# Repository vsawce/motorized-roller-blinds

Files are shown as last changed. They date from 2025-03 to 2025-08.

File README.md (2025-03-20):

# Motorized Roller Blinds
A Raspberry Pi Pico W RP2040-based smart blinds project for my apartment.

I made this for fun as well as to minimize nocturnal light bleed from my apartment's outdoor lights while allowing myself to wake up to sunlight in the morning.

This system integrates with Home Assistant and MQTT, so a dedicated Home Assistant instance with the MQTT add-on is needed

## Build / Upload Instructions
As of this markdown's commit 
### Linux
1. Clone the [pico-sdk](https://github.com/raspberrypi/pico-sdk) and [FreeRTOS-Kernel](https://github.com/FreeRTOS/FreeRTOS-Kernel) repos
    * Follow their instructions for setup
2. If not done already, create the following system variables and assign them to pico-sdk and FreeRTOS-Kernel paths
    * Example in `~/.bashrc`:
      ```
      #PI PICO SDK
      export PICO_SDK_PATH=/home/<user>/pico-sdk/
      export FREERTOS_KERNEL_PATH=/home/<user>/FreeRTOS-Kernel/
      ```
    * `source ~/.bashrc` after
3. Clone this repo
4. `cd` into this repo's root directory
5. `mkdir build`
6. `cd build`
7. Run cmake in this directory
    * **Required options/arguments**:
      * `-DPICO_BOARD=pico_w`
      * `-DWIFI_SSID="<your_wifi_ssid>"`
      * `-DWIFI_PASSWORD="<your_wifi_pass>"`
      * `-DMQTT_CLIENT_ID="<custom_client_id>"`
        * Should be a custom and unique ID for each Pico W device. You choose.
      * `-DMQTT_USER=<"home_assistant_user">`
        * Should be the helper user you created specifically Home Assistant for MQTT
      * `-DMQTT_PASSWORD=<"home_assistant_pass">`
        * Should be the helper user's password you created specifically Home Assistant for MQTT
    * Example call: `cmake -DPICO_BOARD=pico_w -DWIFI_SSID="eduroam" -DWIFI_PASSWORD="abc123" -DMQTT_CLIENT_ID="picow_0" -DMQTT_USER="mqtt_test" -DMQTT_PASSWORD="xyz123" ..`
8. **Ensure the following user-defined macros in the program are correct**
    * definitions.h:
      * In `namespace BLINDS`, make sure your window height and blinds' shaft diameter is set accurately
      * In `namespace PIN`, make sure GPIO pins are set properly
    * wifi.h (may move these to definitions.h in the future):
      * `MQTT_ADDR` - point to the IP your Home Assistant is running on
      * `MQTT_ADDR_PORT` - point to the port your Home Assistant is configured to for MQTT
      * `MQTT_POS_REQUEST_TOPIC` - if you want to set a custom MQTT topic for position request (I use `/blinds/<MQTT_CLIENT_ID>/pos_request`)
      * `MQTT_POS_JSON_KEY` - JSON key string for Home Assistant -> Pico W blinds % position command (My example json: `{"pos":"50%"}`)
9. `make main` to build once all variables are set
10. Copy `src/main.uf2` into your Pico W and start a serial terminal!

## Home Assistant Example Config
As of Home Assistant Core 2025.3.3 and Home Assistant Operating System 15.0 
</br>
* After installing MQTT add-on and creating a dedicated Home Assistant user for MQTT:
  * Settings->Devices & services->MQTT
  * Click the three dots next to the Mosquitto integration entry->Reconfigure
  * Ensure port is set correctly, and then add the dedicated MQTT Home Assistant user's credentials
  * Submit
* Use something like the Studio Code Server add-on to edit `/config/configuration.yaml` (my current config):
  * ```
    # Loads default set of integrations. Do not remove.
    default_config:
    
    # Load frontend themes from the themes folder
    frontend:
      themes: !include_dir_merge_named themes
    
    automation: !include automations.yaml
    script: !include scripts.yaml
    scene: !include scenes.yaml
    
    input_number:
      slider1:
        name: Bedroom Blinds
        initial: 0
        min: 0
        max: 100
        step: 5
    mqtt:
      - cover:
          name: Smart Blinds
          unique_id: smart__blinds
          command_topic: "/blinds/picow_0/command"
          position_topic: "/blinds/picow_0/pos_status"
          set_position_topic: "/blinds/picow_0/pos_req"
          payload_open: "100"
          payload_close: "0"
          position_open: 100
          position_closed: 0
    ```
* Set up an automation with similar YAML:
  * ```
    - id: <AUTO_ASSIGNED_BY_HOMEASSISTANT?>
    alias: Adjust Blinds Position
    description: ""
    triggers:
      - trigger: state
        entity_id: input_number.slider1
    conditions: []
    actions:
      - action: mqtt.publish
        data_template:
          qos: "0"
          topic: "/blinds/picow_0/pos_request"
          payload: "{\"pos\":\"{{ states('input_number.slider1') | int }}%\"}"
    mode: single
    ```

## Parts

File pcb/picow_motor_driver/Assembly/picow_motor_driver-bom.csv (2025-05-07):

Comment | Designator | Footprint | JLCPCB Part #（optional）
10nF | C1 | Capacitor_SMD:C_0603_1608Metric | C1589
LED | D1,D2,D3,D4 | LED_SMD:LED_0603_1608Metric | C965799
470 | R1,R2,R3,R4 | Resistor_SMD:R_0603_1608Metric | C23179
10k | R5,R6,R7 | Resistor_SMD:R_0603_1608Metric | C25804
TS-1088-AR02016 | SW1,SW2,SW3 | Library:SW-SMD_L3.9-W3.0-P4.45 | C720477
ULN2003D1013TR | U2 | Library:SOIC-16_L9.9-W3.9-P1.27-LS6.0-BL | C61273
920-E52A2021S10100 | USB1 | Library:MICRO-USB-SMD_5P-P0.65-H-F_C10418 | C10418

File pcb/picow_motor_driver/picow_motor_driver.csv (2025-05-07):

Reference | Value | Footprint | Datasheet | Qty | DNP | Exclude from BOM | Exclude from Board
C1 | 10nF | Capacitor_SMD:C_0603_1608Metric | ~ | 1
D1,D2,D3,D4 | LED | LED_SMD:LED_0603_1608Metric | ~ | 4
J1 | Conn_01x02_Pin | Connector_PinHeader_2.54mm:PinHeader_1x02_P2.54mm_Vertical | ~ | 1
J2 | Conn_01x05_Pin | Connector_PinHeader_2.54mm:PinHeader_1x05_P2.54mm_Horizontal | ~ | 1
J3 | Conn_01x04_Pin | Connector_PinSocket_2.54mm:PinSocket_1x04_P2.54mm_Horizontal | ~ | 1
R1,R2,R3,R4 | 470 | Resistor_SMD:R_0603_1608Metric | ~ | 4
R5,R6,R7 | 10k | Resistor_SMD:R_0603_1608Metric | ~ | 3
SW1,SW2,SW3 | ~ | Library:SW-SMD_L3.9-W3.0-P4.45 | https://atta.szlcsc.com/upload/public/pdf/source/20200810/C720475_60D09DD6C54279ADDB2DC25100F1CC11.pdf | 3
U1 | Pico | Library:RPi_Pico_SMD_TH |  | 1
U2 | ~ | Library:SOIC-16_L9.9-W3.9-P1.27-LS6.0-BL | https://atta.szlcsc.com/upload/public/pdf/source/20171116/C93000_15108227945891124497.pdf | 1
USB1 | ~ | Library:MICRO-USB-SMD_5P-P0.65-H-F_C10418 | https://atta.szlcsc.com/upload/public/pdf/source/20210305/C10418_4890444E73C7CF5EB311058F76E5ECA4.pdf | 1

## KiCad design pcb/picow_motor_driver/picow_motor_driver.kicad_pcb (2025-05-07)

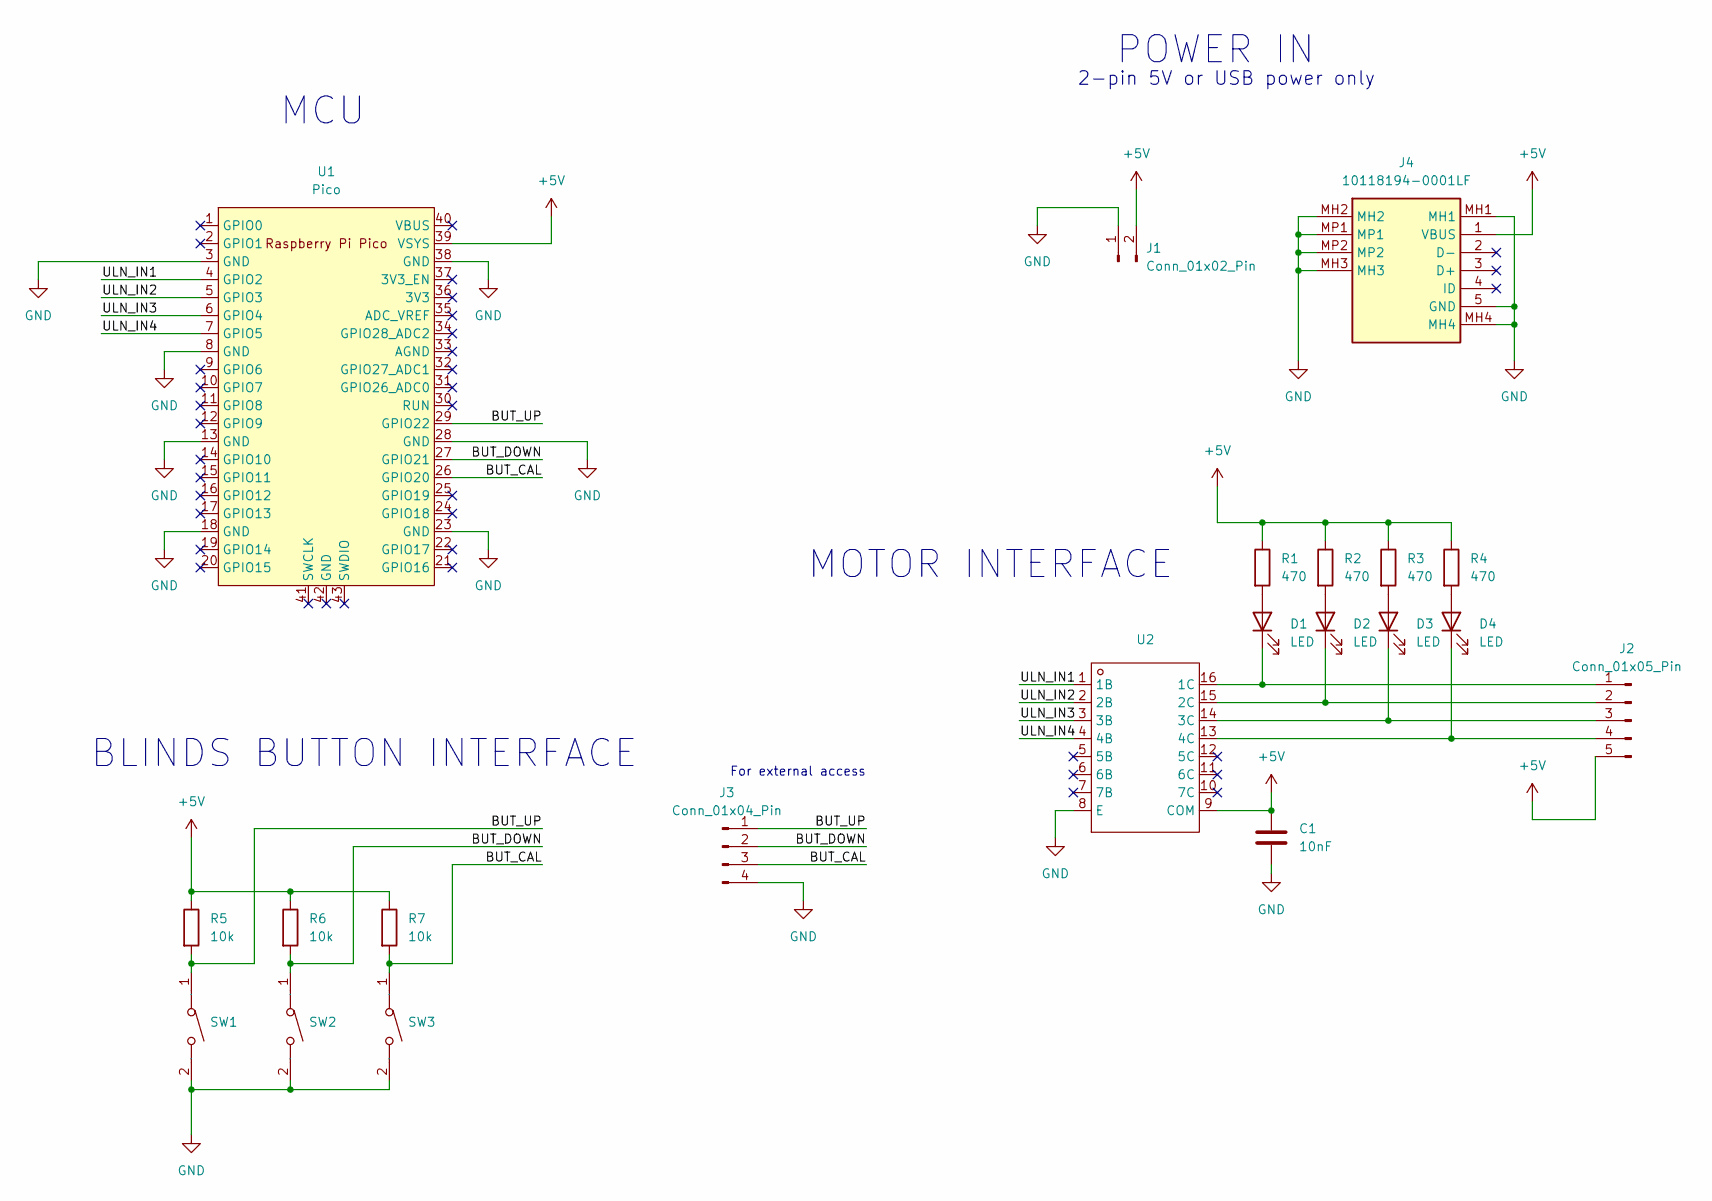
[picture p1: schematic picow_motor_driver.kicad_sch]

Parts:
C1: 10nF; C_0603_1608Metric
D1, D2, D3, D4: LED; LED_0603_1608Metric
J1: Conn_01x02_Pin; PinHeader_1x02_P2.54mm_Vertical
J2: Conn_01x05_Pin; S5B-XH-A
J3: Conn_01x04_Pin; S4BXHALFSN
J4: 10118194-0001LF; 101181940001LF; Manufacturer_Part_Number 10118194-0001LF
R1, R2, R3, R4: 470; R_0603_1608Metric
R5, R6, R7: 10k; R_0603_1608Metric
SW1, SW2, SW3: SW-SMD_L3.9-W3.0-P4.45; Manufacturer Part TS-1088-AR02016; LCSC Part Name 4*3*2mm 立贴 轻触开关
U1: Pico; RPi_Pico_SMD_TH
U2: SOIC-16_L9.9-W3.9-P1.27-LS6.0-BL; Manufacturer Part ULN2003D1013TR; LCSC Part Name ULN2003D1013TR

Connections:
+5V: C1.1, J1.2, J2.5, J4.1 (VBUS), R1.1, R2.1, R3.1, R4.1, R5.1, R6.1, R7.1, U1.39 (VSYS), U2.9 (COM)
/BUT_CAL: J3.3, R7.2, SW3.1, U1.26 (GPIO20)
/BUT_DOWN: J3.2, R6.2, SW2.1, U1.27 (GPIO21)
/BUT_UP: J3.1, R5.2, SW1.1, U1.29 (GPIO22)
/ULN_IN1: U1.4 (GPIO2), U2.1 (1B)
/ULN_IN2: U1.5 (GPIO3), U2.2 (2B)
/ULN_IN3: U1.6 (GPIO4), U2.3 (3B)
/ULN_IN4: U1.7 (GPIO5), U2.4 (4B)
GND: C1.2, J1.1, J3.4, J4.5 (GND), J4.MH1, J4.MH2, J4.MH3, J4.MH4, J4.MP1, J4.MP2, SW1.2, SW2.2, SW3.2, U1.3 (GND), U1.8 (GND), U1.13 (GND), U1.18 (GND), U1.23 (GND), U1.28 (GND), U1.38 (GND), U2.8 (E)
unnamed: D1.2 (A), R1.2
unnamed: D1.1 (K), J2.1, U2.16 (1C)
unnamed: D2.2 (A), R2.2
unnamed: D2.1 (K), J2.2, U2.15 (2C)
unnamed: D3.2 (A), R3.2
unnamed: D3.1 (K), J2.3, U2.14 (3C)
unnamed: D4.2 (A), R4.2
unnamed: D4.1 (K), J2.4, U2.13 (4C)

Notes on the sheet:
POWER IN
BLINDS BUTTON INTERFACE
2-pin 5V or USB power only
MCU
For external access
MOTOR INTERFACE

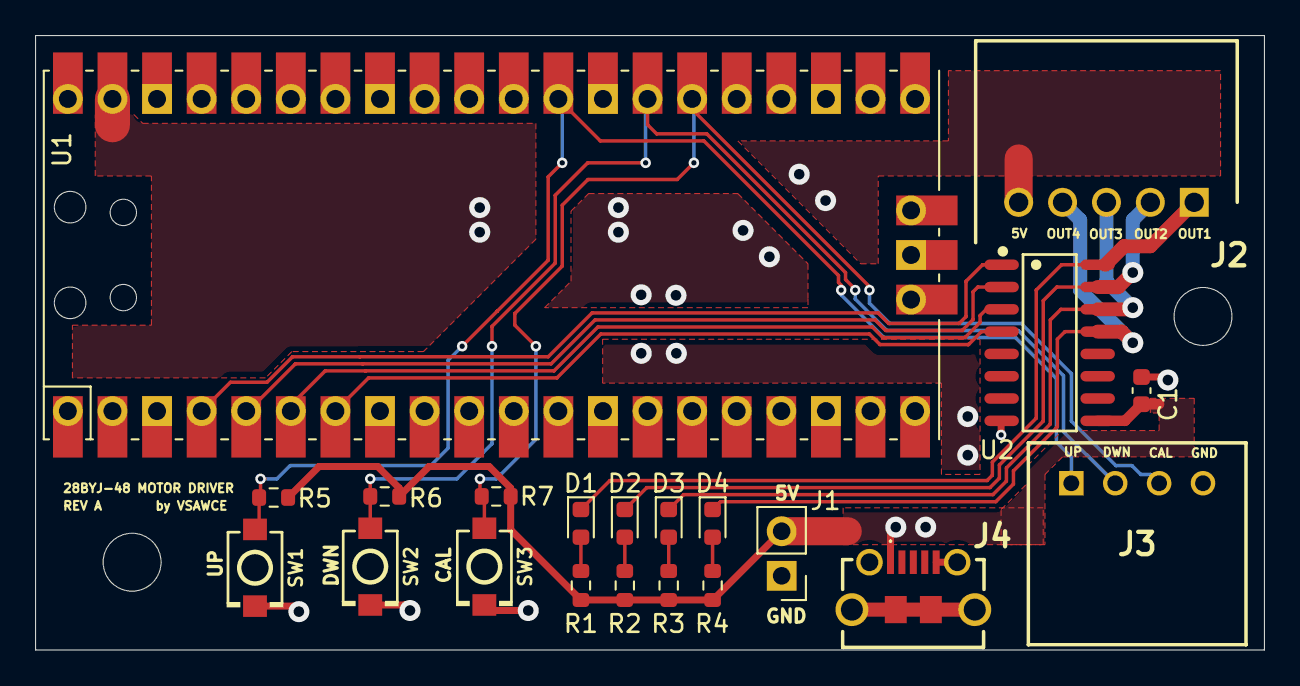
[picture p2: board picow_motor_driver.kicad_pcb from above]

Board: 2 copper layers, 70.0 x 35.0 mm, 21 parts (0 on the bottom side), 17 nets.

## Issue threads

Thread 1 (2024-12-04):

Add/test motor control in reverse direction

vsawce, 2024-12-04:

vsawce, 2024-12-09:
Added with 207ea58

Closed 2024-12-09.

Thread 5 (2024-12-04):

Finalize Google Home integration methodology

vsawce, 2024-12-04:
Pi Pico W <-> IFTTT HTTP <-> Google Home?

vsawce, 2025-03-14:
Pi Pico W (lwIP MQTT) <-> MQTT Broker (Home server) <-> Google Home

Closed 2025-03-14.

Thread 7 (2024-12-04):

RTOS Conversion and Multithreading

vsawce, 2024-12-04:
Run WiFi tasks as well as motor drives on separate threads

vsawce, 2025-01-13:
Gotta figure out allocation of functionalities between cores as well, as well as priorities

vsawce, 2025-02-12:
Good enough for now. Bound logger to 1st core, and blink/motor to 2nd core. Left wifi ambiguous as binding it throws assertions/panics, but it usually starts on the 1st core

Closed 2025-02-12.

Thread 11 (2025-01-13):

Basic WiFi functionality

vsawce, 2025-01-13:
Test ping to 8.8.8.8 (google) or something

vsawce, 2025-01-27:
[5fd85c7](https://github.com/vsawce/motorized-roller-blinds/commit/5fd85c7c6ad207df2d6783b920fc79bf568ae20f) didn't actually fix panic in NO_SYS=0 mode. Sometimes it triggers intermittently.

Potential workaround is to allow wifi initialization tasks to go first before launching other ones.

vsawce, 2025-01-27:
cyw43_arch_init must go first apparently (therefore moved wifi task to start first)? Otherwise, panics/assertions are thrown such as `assertion "!(raw_irq_mask[get_core_num()] & gpio_mask)" failed`. Need to investigate.

Closed 2025-02-12.

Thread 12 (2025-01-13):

Add USB/UART debug interface

vsawce, 2025-01-13:
Can be related to #8.

Need to figure out how to allocate this functionality to one of the two cores #7.

vsawce, 2025-01-15:
Add runtime printout!

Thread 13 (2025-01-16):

Thermistor to sense motor temperature

vsawce, 2025-01-16:
Enact shutoffs if too hot?

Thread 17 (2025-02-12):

Button debouncing

vsawce, 2025-02-12:
Related to #3. Also good to practice again

vsawce, 2025-02-25:
Integrated button actions to motor task, and debouncing probably not needed as lazy button read or motor command processing delays should be good enough as a replacement

Closed 2025-02-25.

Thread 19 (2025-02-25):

Add watchdog/timer for purpose of releasing motor

vsawce, 2025-02-25:
Add a watchdog/timer to monitor if the motor command queue hasn't received any new commands after a fixed time interval, then send a release/stop command

vsawce, 2025-02-28:
Done

Closed 2025-02-28.

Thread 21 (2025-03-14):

Implement MQTT to connect with MQTT broker on HAOS instance

vsawce, 2025-03-14:
Related: #5

Pi Pico W (lwIP MQTT) <-> MQTT Broker (Home server) <-> Google Home

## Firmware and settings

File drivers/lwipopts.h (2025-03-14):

#ifndef _LWIPOPTS_EXAMPLE_COMMONH_H
#define _LWIPOPTS_EXAMPLE_COMMONH_H


// Common settings used in most of the pico_w examples
// (see https://www.nongnu.org/lwip/2_1_x/group__lwip__opts.html for details)

// allow override in some examples
#ifndef NO_SYS
#define NO_SYS                      1
#endif

#if !NO_SYS
#define TCPIP_THREAD_STACKSIZE 1024
#define DEFAULT_THREAD_STACKSIZE 2048
#define DEFAULT_RAW_RECVMBOX_SIZE 8
#define TCPIP_MBOX_SIZE 8
#define LWIP_TIMEVAL_PRIVATE 0

// not necessary, can be done either way
#define LWIP_TCPIP_CORE_LOCKING_INPUT 1

// ping_thread sets socket receive timeout, so enable this feature
#define LWIP_SO_RCVTIMEO 1
#endif

// allow override in some examples
#ifndef LWIP_SOCKET
#define LWIP_SOCKET                 0
#endif
#if PICO_CYW43_ARCH_POLL
#define MEM_LIBC_MALLOC             1
#else
// MEM_LIBC_MALLOC is incompatible with non polling versions
#define MEM_LIBC_MALLOC             0
#endif
#define MEM_ALIGNMENT               4
#define MEM_SIZE                    4000
#define MEMP_NUM_TCP_SEG            32
#define MEMP_NUM_ARP_QUEUE          10
#define PBUF_POOL_SIZE              24
#define LWIP_ARP                    1
#define LWIP_ETHERNET               1
#define LWIP_ICMP                   1
#define LWIP_RAW                    1
#define TCP_WND                     (8 * TCP_MSS)
#define TCP_MSS                     1460
#define TCP_SND_BUF                 (8 * TCP_MSS)
#define TCP_SND_QUEUELEN            ((4 * (TCP_SND_BUF) + (TCP_MSS - 1)) / (TCP_MSS))
#define LWIP_NETIF_STATUS_CALLBACK  1
#define LWIP_NETIF_LINK_CALLBACK    1
#define LWIP_NETIF_HOSTNAME         1
#define LWIP_NETCONN                0
#define MEM_STATS                   0
#define SYS_STATS                   0
#define MEMP_STATS                  0
#define LINK_STATS                  0
// #define ETH_PAD_SIZE                2
#define LWIP_CHKSUM_ALGORITHM       3
#define LWIP_DHCP                   1
#define LWIP_IPV4                   1
#define LWIP_TCP                    1
#define LWIP_UDP                    1
#define LWIP_DNS                    1
#define LWIP_TCP_KEEPALIVE          1
#define LWIP_NETIF_TX_SINGLE_PBUF   1
#define DHCP_DOES_ARP_CHECK         0
#define LWIP_DHCP_DOES_ACD_CHECK    0

#ifndef NDEBUG
#define LWIP_DEBUG                  1
#define LWIP_STATS                  1
#define LWIP_STATS_DISPLAY          1
#endif

#define ETHARP_DEBUG                LWIP_DBG_OFF
#define NETIF_DEBUG                 LWIP_DBG_OFF
#define PBUF_DEBUG                  LWIP_DBG_OFF
#define API_LIB_DEBUG               LWIP_DBG_OFF
#define API_MSG_DEBUG               LWIP_DBG_OFF
#define SOCKETS_DEBUG               LWIP_DBG_OFF
#define ICMP_DEBUG                  LWIP_DBG_OFF
#define INET_DEBUG                  LWIP_DBG_OFF
#define IP_DEBUG                    LWIP_DBG_OFF
#define IP_REASS_DEBUG              LWIP_DBG_OFF
#define RAW_DEBUG                   LWIP_DBG_OFF
#define MEM_DEBUG                   LWIP_DBG_OFF
#define MEMP_DEBUG                  LWIP_DBG_OFF
#define SYS_DEBUG                   LWIP_DBG_OFF
#define TCP_DEBUG                   LWIP_DBG_OFF
#define TCP_INPUT_DEBUG             LWIP_DBG_OFF
#define TCP_OUTPUT_DEBUG            LWIP_DBG_OFF
#define TCP_RTO_DEBUG               LWIP_DBG_OFF
#define TCP_CWND_DEBUG              LWIP_DBG_OFF
#define TCP_WND_DEBUG               LWIP_DBG_OFF
#define TCP_FR_DEBUG                LWIP_DBG_OFF
#define TCP_QLEN_DEBUG              LWIP_DBG_OFF
#define TCP_RST_DEBUG               LWIP_DBG_OFF
#define UDP_DEBUG                   LWIP_DBG_OFF
#define TCPIP_DEBUG                 LWIP_DBG_OFF
#define PPP_DEBUG                   LWIP_DBG_OFF
#define SLIP_DEBUG                  LWIP_DBG_OFF
#define DHCP_DEBUG                  LWIP_DBG_OFF

/* Need to increase MEMP_NUM_SYS_TIMEOUT by one?
 * https://forums.raspberrypi.com/viewtopic.php?t=341914
 */
#define MEMP_NUM_SYS_TIMEOUT   (LWIP_NUM_SYS_TIMEOUT_INTERNAL + 1)
#define MQTT_REQ_MAX_IN_FLIGHT (5)  //max subscribe requests

#endif /* __LWIPOPTS_H__ */

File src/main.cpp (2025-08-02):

/**
 *  Designed by Vincent Saw
 * 
 */
#include <stdio.h>
#include "pico/stdlib.h"
//#include "pico/multicore.h"
#include "pico/cyw43_arch.h"
#include "hardware/watchdog.h"

#include "lwip/ip4_addr.h"

#include "FreeRTOS.h"
#include "task.h"
#include "timers.h"

// Inclusion of C program
#ifdef __cplusplus
extern "C" {
#endif

#include "ping.h"

#ifdef __cplusplus
}
#endif

#include "definitions.h"
#include "led.h"
#include "wifi.h"
#include "motor.h"
#include "logger.h"
#include "button.h"

//##################################//
//          USER MACROS             //
//##################################//

// Which core to run on if configNUMBER_OF_CORES==1
#ifndef RUN_FREE_RTOS_ON_CORE
#define RUN_FREE_RTOS_ON_CORE 0
#endif

// Whether to flash the led
#ifndef USE_LED
#define USE_LED 0
#endif

// Whether to busy wait in the led thread
#ifndef LED_BUSY_WAIT
#define LED_BUSY_WAIT 0
#endif

// Delay between led blinking
#define LED_DELAY_MS    1000
// Watchdog timer duration
#define WDT_DURATION_MS 5000

// Ping google
#ifndef PING_ADDR
#define PING_ADDR "8.8.8.8"
#endif

// Priorities of our threads - higher numbers are higher priority
#define LOGGER_TASK_PRIORITY        ( tskIDLE_PRIORITY + 4UL )  //Highest
#define WIFI_TASK_PRIORITY         ( tskIDLE_PRIORITY + 3UL )
#define MOTOR_TASK_PRIORITY         ( tskIDLE_PRIORITY + 2UL )
#define BLINK_TASK_PRIORITY         ( tskIDLE_PRIORITY + 1UL )  //Lowest

// Stack sizes of our threads in words (4 bytes)
#define LOGGER_TASK_STACK_SIZE      ( configMINIMAL_STACK_SIZE + 128 )
#define WIFI_TASK_STACK_SIZE        ( configMINIMAL_STACK_SIZE + 512 )
#define MOTOR_TASK_STACK_SIZE       ( configMINIMAL_STACK_SIZE + 64 )
#define BLINK_TASK_STACK_SIZE       ( configMINIMAL_STACK_SIZE )

//##################################//
//          ???????????             //
//##################################//

// #include "pico/async_context_freertos.h"
// static async_context_freertos_t async_context_instance;

// // Create an async context
// static async_context_t *example_async_context(void) {
//     async_context_freertos_config_t config = async_context_freertos_default_config();
//     config.task_priority = WORKER_TASK_PRIORITY; // defaults to ASYNC_CONTEXT_DEFAULT_FREERTOS_TASK_PRIORITY
//     config.task_stack_size = WORKER_TASK_STACK_SIZE; // defaults to ASYNC_CONTEXT_DEFAULT_FREERTOS_TASK_STACK_SIZE
//     if (!async_context_freertos_init(&async_context_instance, &config))
//         return NULL;
//     return &async_context_instance.core;
// }

// Thread-safe log sending function
// void send_log(const char *message)
// {
//     if (logQueue != NULL) {
//         if (xQueueSend(logQueue, message, pdMS_TO_TICKS(100)) != pdPASS) {
//             // Handle queue full (optional, TODO?)
//             //printf("Log queue full. Message dropped: %s\n", message); // Add this for debugging
//         }
//     }
// }


//##################################//
//              TASKS               //
//##################################//

///////////////////
// BLINK TASK
///////////////////

//Can remove typedef if in C++ do get similar typedef struct behavior from C

#if USE_LED
void blink_task(void *pvParameters)
{
    if (pvParameters == NULL) {
        //log_send(LogType::ERROR, "Blink task: Invalid parameters");
        vTaskDelete(NULL);  // Delete this task if parameters are invalid
    }

    log_send(LogType::STANDARD, "blink_task started on core %d\n", portGET_CORE_ID());

    LED     *led_ptr = (LED*)pvParameters;

    while (true) {
        led_ptr->toggle();
        log_send(LogType::DEBUG, "Toggled");
        vTaskDelay(pdMS_TO_TICKS(500));
    }

// #if LED_BUSY_WAIT
//         // You shouldn't usually do this. We're just keeping the thread busy,
//         // experiment with BLINK_TASK_PRIORITY and LED_BUSY_WAIT to see what happens
//         // if BLINK_TASK_PRIORITY is higher than TEST_TASK_PRIORITY main_task won't get any free time to run
//         // unless configNUMBER_OF_CORES > 1
//         busy_wait_ms(LED_DELAY_MS);
// #else
//         sleep_ms(LED_DELAY_MS);
// #endif
}
#endif // USE_LED

///////////////////
//  MOTOR TASK
///////////////////

//  Timer callback function must match the prototype:
//      void vCallbackFunctionExample( TimerHandle_t xTimer );
void vTimerCallback_ReleaseMotor(TimerHandle_t xTimer)
{
    Motor::releaseMotor();
}

void motor_task(void *pvParameters)
{
    if (pvParameters == NULL) {
        //log_send(LogType::ERROR, "Motor task: Invalid parameters");
        vTaskDelete(NULL);  // Delete this task if parameters are invalid
    }

    log_send(LogType::STANDARD, "motor_task started on core %d\n", portGET_CORE_ID());

    Motor *mtr_ptr = (Motor*)pvParameters;

    Button b;

    b.init();

    // Create RTOS timer object to release motor
    TimerHandle_t motorReleaseTimerHandle;
    motorReleaseTimerHandle = xTimerCreate("MotorReleaseTimer", pdMS_TO_TICKS(MOTOR_RELEASE_TIMEOUT_MS), pdFALSE, (void*) 0, vTimerCallback_ReleaseMotor);

    while (true) {
        // Test code to rotate the shaft back and forth
        // mtr_ptr->rotateToPercent(0);
        // vTaskDelay(pdMS_TO_TICKS(1000));

        // mtr_ptr->rotateToPercent(50);
        // vTaskDelay(pdMS_TO_TICKS(1000));

        // mtr_ptr->rotateToPercent(100);
        // vTaskDelay(pdMS_TO_TICKS(1000));

        // mtr_ptr->rotateToPercent(50);
        // vTaskDelay(pdMS_TO_TICKS(1000));
        b.update(mtr_ptr);
        if (mtr_ptr->processCommands(motorReleaseTimerHandle)) {
            xTimerStart(motorReleaseTimerHandle, 0);
        }

        vTaskDelay(pdMS_TO_TICKS(10));
    }

}

///////////////////
//  LOGGER TASK
///////////////////

void logger_task(__unused void *pvParameters)
{
    log_send(LogType::STANDARD, "logger_task started on core %d\n", portGET_CORE_ID());

    while (true) {
        log_receive(); //Consume log in queue and print it
    }
}

///////////////////
// WIFI TASK
///////////////////

// void mqtt_connection_cb(mqtt_client_t* client, void* arg, mqtt_connection_status_t status) {
//     err_t err;
//     if (status == MQTT_CONNECT_ACCEPTED) {
//         log_send(LogType::STANDARD, "mqtt_connection_cb: Successfully connected\n");
//     } 
//     else {
//       log_send(LogType::STANDARD, "mqtt_connection_cb: Disconnected, reason: %d\n", status);
  
//       /* Its more nice to be connected, so try to reconnect */
//       //mqtt_connect(client);
//     }
// }
  

void wifi_task(void *pvParameters)
{
    if (pvParameters == NULL) {
        // printf("Motor task: Invalid parameters");
        vTaskDelete(NULL);  // Delete this task if parameters are invalid
    }

    LED led;
    Motor mtr(PIN::ULN2003_IN1, PIN::ULN2003_IN2, PIN::ULN2003_IN3, PIN::ULN2003_IN4, MotorDriveMode::NormalDrive);
    mtr.init();

    if (watchdog_caused_reboot()) {
        printf("Rebooted by Watchdog?\n");
    } else {
        printf("Clean boot\n");
    }

    //If WDT not updated for WDT_DURATION_MS + wifi timeout ms, reset. 2nd arg = 1 = pause during debug
    watchdog_enable((WDT_DURATION_MS+CYW43::WIFI_TIMEOUT_MS), 1); 

    //printf("\"BLINDS::WINDOW_HEIGHT_MM\":%dmm\t\"getWindowHeightLimitSteps()\": %dsteps\n", BLINDS::WINDOW_HEIGHT_MM, mtr.getWindowHeightLimitSteps());

    log_send(LogType::STANDARD, "wifi_task started on core %d\n", portGET_CORE_ID());

    Wifi    *wifi_ptr   = (Wifi*)pvParameters;

    log_send(LogType::STANDARD, "Initializing wifi...\n");
    if (wifi_ptr->init(&mtr)) {
        log_send(LogType::ERROR, "Failed to init CYW43 Wifi & LED\n");
    }

    watchdog_update(); //Update WDT

    log_send(LogType::STANDARD, "Enabling WiFi station mode...\n");
    wifi_ptr->enableStationMode();

    watchdog_update(); //Update WDT
    
    log_send(LogType::STANDARD, "Connecting to wifi SSID %s ...\n", WIFI_SSID);
    int err;
    //Loop while there is an error present
    do {
        err = wifi_ptr->connectToWifi(WIFI_SSID, WIFI_PASSWORD, CYW43_AUTH_WPA2_AES_PSK, CYW43::WIFI_TIMEOUT_MS);
        if (err) {
            log_send(LogType::ERROR, "Failed to connect to wifi SSID %s, timeout: %ums | Err code %d\n", WIFI_SSID, CYW43::WIFI_TIMEOUT_MS, err);
            log_send(LogType::STANDARD, "Trying again...\n");
        }
    } while (err);

    log_send(LogType::STANDARD, "Connected to wifi SSID %s !\n", WIFI_SSID);
    log_send(LogType::STANDARD, "Assigned IP is: %s\n", ip4addr_ntoa(netif_ip4_addr(netif_list)));

    watchdog_update(); //Update WDT

    wifi_ptr->initMqtt();

    watchdog_update(); //Update WDT

    wifi_ptr->connectMqtt();

    ////////

    watchdog_update(); //Update WDT

    watchdog_disable(); //Stop WDT as problematic section is in wifi

    vTaskDelay(1000);

    TaskHandle_t logger_task_handle;
    xTaskCreate(logger_task, "LoggerTask", LOGGER_TASK_STACK_SIZE, NULL, LOGGER_TASK_PRIORITY, &logger_task_handle);
    vTaskCoreAffinitySet(logger_task_handle, 0x1); //Set logger_task to 1st core

#if USE_LED
    //Init LED
    TaskHandle_t blink_task_handle;
    xTaskCreate(blink_task, "BlinkTask", BLINK_TASK_STACK_SIZE, &led, BLINK_TASK_PRIORITY, &blink_task_handle);
    vTaskCoreAffinitySet(blink_task_handle, 0x2); //Set blink_task to 2nd core
#endif

    TaskHandle_t motor_task_handle;
    xTaskCreate(motor_task, "MotorTask", MOTOR_TASK_STACK_SIZE, &mtr, MOTOR_TASK_PRIORITY, &motor_task_handle);
    vTaskCoreAffinitySet(motor_task_handle, 0x2); //Set motor_task to 2nd core

    
    log_send(LogType::STANDARD, "Pinging %s\n", PING_ADDR);
    ip_addr_t ping_addr;
    ipaddr_aton(PING_ADDR, &ping_addr);
    ping_init(&ping_addr);
    
    
    while(true) {
        // not much to do as LED is in another task, and we're using RAW (callback) lwIP API
        vTaskDelay(100);
    }

    cyw43_arch_deinit();
}


//##################################//
//              MAIN                //
//##################################//
int main()
{
    Wifi wifi;

    if (log_init()) printf("Failed to initialize logger\n");

    // Create the Wi-Fi task on Core 0
    TaskHandle_t wifi_task_handle;
    xTaskCreate(wifi_task, "WifiTask", WIFI_TASK_STACK_SIZE, &wifi, WIFI_TASK_PRIORITY, &wifi_task_handle);

    // Set the task to run on Core 1
    // vTaskCoreAffinitySet(wifi_task_handle, 0x1);  // Bind the Wi-Fi task to 2nd core

    // Start the scheduler
    vTaskStartScheduler();

} 

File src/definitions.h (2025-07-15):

#ifndef DEFINITIONS_H
#define DEFINITIONS_H

#include "pico/stdlib.h"

//////////////////////////
//  CYW43 PARAMETERS    //
//////////////////////////

namespace CYW43
{
    constexpr int WIFI_TIMEOUT_MS = 30000; //30s timeout
}

//////////////////////////
//  BLIND PARAMETERS    //
/////////////////////////

namespace BLINDS
{
    constexpr uint8_t SHAFT_DIAMETER_MM = 40;               // ~4cm shaft
    constexpr uint16_t WINDOW_HEIGHT_MM = 1778 + 120;       // 70 inch window (1778mm) + ~5 in buffer
}

//////////////
//  PINS    //
//////////////

namespace PIN
{ 
    // constexpr for compile-time evalutation (modern C++?)
    constexpr uint8_t ULN2003_IN1   = 2;    //GPIO2
    constexpr uint8_t ULN2003_IN2   = 3;    //GPIO3
    constexpr uint8_t ULN2003_IN3   = 4;    //GPIO4
    constexpr uint8_t ULN2003_IN4   = 5;    //GPIO5

    constexpr uint8_t BUTTON_UP     = 22;   //GPIO22, move blinds up
    constexpr uint8_t BUTTON_DOWN   = 21;   //GPIO21, move blinds down
    constexpr uint8_t BUTTON_CALIB  = 20;   //GPIO20, calibrate blind position
}

namespace CYW43_PIN
{
    constexpr uint8_t LED = 0;
}



#endif

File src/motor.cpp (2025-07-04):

#include "motor.h"

constexpr uint16_t PI_TIMES_100 = 314; //Integer to skip FP math

constexpr uint8_t MAX_PERCENT = 100; //Constant for rotateToPercent

//  NORMAL DRIVE (more power, more torque)
//  -----------
//   0     1001 0x9
//   1     1100 0xC
//   2     0110 0x6
//   3     0011 0x3
constexpr uint8_t normalDriveStepSequence[4] = {0x9, 0xC, 0x6, 0x3};
// constexpr uint8_t normalDriveStepSequence[4] = {0x3, 0x6, 0xC, 0x9};

//  WAVE DRIVE (less power, but less torque)
//  -----------
//   Phase DCBA Val
//   0     1000 0x8
//   1     0100 0x4
//   2     0010 0x2
//   3     0001 0x1
constexpr uint8_t waveDriveStepSequence[4] = {0x8, 0x4, 0x2, 0x1};
// constexpr uint8_t waveDriveStepSequence[4] = {0x1, 0x2, 0x4, 0x8};

//  HALF STEP DRIVE (Slower, but more accuracy)
//  -----------
//   Phase DCBA Val
//   0     1001 0x9
//   1     1000 0x8
//   2     1100 0xC
//   3     0100 0x4
//   4     0110 0x6
//   5     0010 0x2
//   6     0011 0x3
//   7     0001 0x1
constexpr uint8_t halfStepDriveStepSequence[8] = {0x9, 0x8, 0xc, 0x4, 0x6, 0x2, 0x3, 0x1};
// constexpr uint8_t halfStepDriveStepSequence[8] = {0x1, 0x3, 0x2, 0x6, 0x4, 0xc, 0x8, 0x9};

constexpr uint8_t NUM_PINS = 4;

//  5.625 deg / 64 steps
//  (360 deg / 1 full rev) * (64 steps / 5.625 deg) = 64 * 64 = 2048 steps per full rev
constexpr uint16_t STEPS_PER_FULL_REV = 2048;

////////////////////////////////


uint8_t pinIn[4];

Motor::Motor(uint8_t pinIn1, uint8_t pinIn2, uint8_t pinIn3, uint8_t pinIn4, MotorDriveMode dm)
{
    // m_fSteps = fSteps;
    pinIn[0] = pinIn1;
    pinIn[1] = pinIn2;
    pinIn[2] = pinIn3;
    pinIn[3] = pinIn4;

    if (dm == MotorDriveMode::NormalDrive) {
        m_driveMode = normalDriveStepSequence;
        m_numPhases = 4;
        m_numStepsPerFullRotation = STEPS_PER_FULL_REV;
    }
    else if (dm == MotorDriveMode::WaveDrive) {
        m_driveMode = waveDriveStepSequence;
        m_numPhases = 4;
        m_numStepsPerFullRotation = STEPS_PER_FULL_REV;
    }
    else { //Half Step Drive
        m_driveMode = halfStepDriveStepSequence;
        m_numPhases = 8; //Half the speed
        m_numStepsPerFullRotation = STEPS_PER_FULL_REV*2;
    }

    m_currentStepPos = 0;

    //Turn linear window height to max # of steps
    m_windowHeightLimitSteps = (m_numStepsPerFullRotation * 100 * BLINDS::WINDOW_HEIGHT_MM) / (BLINDS::SHAFT_DIAMETER_MM * PI_TIMES_100);
}

// uint8_t Motor::getDriveMode()
// {
//     return *m_driveMode;
// }

uint8_t Motor::getNumPhases()
{
    return m_numPhases;
}

uint16_t Motor::getNumStepsPerFullRotation()
{
    return m_numStepsPerFullRotation;
}

uint32_t Motor::getCurrentStepPos()
{
    return m_currentStepPos;
}

uint32_t Motor::getWindowHeightLimitSteps()
{
    return m_windowHeightLimitSteps;
}

QueueHandle_t Motor::getCommandQueue()
{
    return m_commandQueue;
}

void Motor::init()
{
    for (uint8_t i = 0; i < NUM_PINS; i++) //4 GPIO
    {
        gpio_init(pinIn[i]);
        gpio_set_dir(pinIn[i], GPIO_OUT);
    }

    m_commandQueue = xQueueCreate(CMD_QUEUE_SIZE, sizeof(MotorCommandMessage));
    if (m_commandQueue == NULL) {
        log_send(LogType::ERROR, "Failed to create cmd queue\n");
        return;
    }
}

uint8_t Motor::processCommands(TimerHandle_t mr_th)
{
    uint8_t commandProcessed = 0;
    MotorCommandMessage cmd;

    while (xQueueReceive(m_commandQueue, &cmd, 0) == pdTRUE) {
        commandProcessed = 1; //At least one command was processed
        switch (cmd.mc) {
            case MotorCommand::ROTATE_TO_PERCENT:
                rotateToPercent(cmd.pos);
                break;
            case MotorCommand::BUTTON_UP:
                rotateNumSteps(MotorDriveDirection::Forward, BUTTON_STEPS_PER_UPDATE, true); //Rotate # steps based on user-def macro
                break;
            case MotorCommand::BUTTON_DOWN:
                rotateNumSteps(MotorDriveDirection::Reverse, BUTTON_STEPS_PER_UPDATE, true); //Rotate # steps based on user-def macro
                break;
            case MotorCommand::CALIBRATE:
                calibrateCurrentStepPosZero();
                vTaskDelay(pdMS_TO_TICKS(250)); //Lazy delay to eliminate need for calibration button debounce
                break;
        }
    }

    return commandProcessed;
}

void Motor::set_step(uint8_t phase)
{
    if (phase < m_numPhases) { //Valid phase number
        for (uint8_t i = 0; i < NUM_PINS; i++) {
            gpio_put(pinIn[i], (m_driveMode[phase] >> i) & 1);
        }
    }
}

void Motor::calibrateCurrentStepPosZero()
{
    m_currentStepPos = 0;
    log_send(LogType::STANDARD, "Calibrated, set current step pos to 0");
}

void Motor::rotateNumSteps(MotorDriveDirection dir, uint32_t numSteps, bool disable_limit)
{
    if (disable_limit) {
        if (dir == MotorDriveDirection::Forward) {
            for (uint16_t pos = 0; pos < numSteps; pos++) {
                m_currentStepPos++;
                set_step(pos % m_numPhases);
                vTaskDelay(pdMS_TO_TICKS(MOTOR_DRIVE_SPEED_MS_FORWARD));
            }
        }
        else {
            for (uint16_t pos = numSteps; pos > 0; pos--) {
                m_currentStepPos--;
                set_step(pos % m_numPhases);
                vTaskDelay(pdMS_TO_TICKS(MOTOR_DRIVE_SPEED_MS_REVERSE));
            }
        }
    }
    else {
        if (dir == MotorDriveDirection::Forward) {
            for (uint16_t pos = 0; pos < numSteps; pos++) {
                if (m_currentStepPos == m_windowHeightLimitSteps) {
                    log_send(LogType::STANDARD, "Max window height reached! Current/max pos: %u steps\n", m_currentStepPos);
                    break;
                }
                m_currentStepPos++;
                set_step(pos % m_numPhases);
                vTaskDelay(pdMS_TO_TICKS(MOTOR_DRIVE_SPEED_MS_FORWARD));
            }
        }
        else {
            for (uint16_t pos = numSteps; pos > 0; pos--) {
                if (m_currentStepPos == 0) {
                    log_send(LogType::STANDARD, "Min window retraction reached! Current pos is zero!\n");
                    break;
                }
                m_currentStepPos--;
                set_step(pos % m_numPhases);
                vTaskDelay(pdMS_TO_TICKS(MOTOR_DRIVE_SPEED_MS_REVERSE));
            }
        }
    }
}

void Motor::rotateNumFullRotations(MotorDriveDirection dir, uint8_t numRotations)
{
    rotateNumSteps(dir, m_numStepsPerFullRotation*numRotations);
}
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

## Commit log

2024-09-28 Added CYW43 wifi driver and updated CMakeList to accomodate
2024-09-28 Added modular topology to blink LED
2024-12-04 Added motor and motor controller datasheet
2024-12-04 Added motor/motor controller pin definitions
2024-12-04 Added terribly crude but functioning motor proof-of-concept code
2024-12-04 Added code to test one full shaft rotation
2024-12-09 Added reverse motor drive direction functionality
    [main.cpp, motor.cpp, motor.h]
2025-01-13 #7: Made LED blink in first step of RTOS conversion
2025-01-13 Added LED toggle macro in main function
2025-01-13 Minimally functional test code to blink LED while driving motor
2025-01-15 #12: Added queue-based USB debug task prototype
2025-01-16 Slightly adjusted white-space and curly bracket formatting
2025-01-16 Added # of full shaft rotations function for RTOS
2025-01-17 #15: Added motor control based on # steps
2025-01-17 #15: Added motor control based on linear distance
2025-01-17 Removed old blocking test functions for motor
2025-01-17 #2: Added var for current pos and calculation of steps based on window height
2025-01-17 Grab numeric limit based on numStepsToRotate's type rather than fixed uint32_t
    [motor.cpp]
2025-01-18 #2: Added rotateToPercent function to move to a percentage based on window height + some test code in motor_task
2025-01-18 Added printf style usage for Logger::send() and added timestamp prefix
2025-01-23 #11: Panic/asserts during init - need to fix. Code broken
    [definitions.h, main.cpp]
2025-01-27 #11: Fixed panic in NO_SYS=1 mode
    [main.cpp]
2025-01-27 #11: Fixed panic in NO_SYS=0 mode
    [lwipopts.h]
2025-01-27 Feed Logger object into motor task struct instead of motor direction
2025-01-27 Removed unused motor direction var
2025-01-27 #11: Improved hard assert panic aversion on startup by moving motor and blink task creation to wifi_task but still needs fixing
    [main.cpp]
2025-01-27 Added core # printout per task
2025-01-27 #11: Fixed assertion/panic issues for real? Moved logger task to initialize 2nd instead of first
    [main.cpp]
2025-01-30 #11: Added IP printout
2025-02-04 Added current list directory
2025-02-04 #11: Fixed ping.c include as this project is CPP
    [main.cpp]
2025-02-12 #3: Added button pin definitions
2025-02-12 #3: Added basic button GPIO interface for up, down, and calibration
2025-02-13 #18 & #3: Crude motor action based on button action
2025-02-25 #3: First rev of button-based manual motor control
2025-02-25 Added motor GPIO release function that can reduce idle power
2025-02-25 #3, #4: Added calibration to 0 by button
2025-02-25 #17: Added lazy delay on calibration command to eliminate need for debouncing
2025-02-25 #20: Adapter motor functions from printf to log_send
2025-02-28 #19: Used FreeRTOS timer to release motor x ms after motor command
2025-03-14 #21: Added MQTT broker connection and related infra
    [lwipopts.h, main.cpp, wifi.cpp]
2025-03-17 #21: Added publish debug print
2025-03-19 Motor ptr passable into wifi class in order to add to queue
2025-03-20 Connected wifi mqtt logic to motor and works. Let's goooooooooooooooo
2025-05-06 Rev A of PCB
    [picow_motor_driver-B_Cu.gbl, picow_motor_driver-B_Mask.gbs, picow_motor_driver-B_Paste.gbp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]
2025-05-07 Changed connectors out to JST, switched USB conn
    [picow_motor_driver-B_Cu.gbl, picow_motor_driver-B_Mask.gbs, picow_motor_driver-B_Paste.gbp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]
2025-07-04 Swapped motor directions
2025-07-04 Add limit bypass using buttons
2025-07-04 Motor drive speed params
2025-07-16 turn led off
2025-07-16 Fix timeout not being fed
    [wifi.cpp]
2025-07-16 Turn back on LED as it breaks init
2025-08-02 Disable led
